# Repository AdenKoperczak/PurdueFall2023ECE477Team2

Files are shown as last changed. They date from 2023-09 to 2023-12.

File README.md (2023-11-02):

# PurdueFall2023ECE477Team2
Code and other files for a desktop Skee-Ball Machine. Our team website can be
found at [https://engineering.purdue.edu/477grp2/](https://engineering.purdue.edu/477grp2/).

# Purdue ECE47700 - Digital Systems Senior Project
This class involves designing a electronics project that could be sold as a 
product. Such a product must involve either a microcontroller or FPGA. More
information can be found at [https://engineering.purdue.edu/ece477/](https://engineering.purdue.edu/ece477/).

# Git Folders and Files
The files in our Git Repository can be broken into two sections: electrical and
code. Electrical design was done in KiCAD 7.0 and includes both schematics and
PCB layouts. Code was done using SystemWorkbench. There are also some other 
code and support files. Bellow is a description of each folder and what it
contains along with some soport files files.

## General Files
- Used Resources.txt: This contains what parts of the microcontroller are being
                      used for what.

## Electrical
- Audio AMP: Contains initial design for our audio amplifier.
- Schematic: Contains the overall schematic and PCB for our design.
- power control: Contains the initial design for our power circuitry.
- sensor: Contains the initial design for our laser break circuit.

## Microcontroller Code
- HUB75Lib: This contains a library and test code to run a 32x64 HUB75 display
            including a font library.
- WS2812BLib: This contains a library and test code for running a WS2812B LED strip.
- SoundLib: This contains a library and test code for generating and playing audio.

## Other Code
- HUB75Font\_Generate: This contains code for generating a font library for the
                       HUB75Lib.

# Project Description
Our project aims to rekindle the nostalgic joy of the traditional Skee-Ball game while
incorporating cutting-edge technology for an enhanced playing experience in the form of
game modes, normal, time attack, and streak. The normal game mode is the same 
as the traditional skate-ball game mode, such that a player would get nine balls and attempt
to score the highest score possible at their own pace, for which the scores per ball are
simply added to get the final score. After they run out of nine balls, any ball they try
to score after would not count, as the game would be over. In time attack mode, the
player sets a time (up to 5 minutes) with an unlimited ball count to score as high as
possible. For the streak mode, the player gets an "unlimited" number of balls as long as
as they score 20 points or higher on the current shot; Once they miss the shot, the score
is finalized. Finally, the timed streak mode combines the time attack with a score.
multiplier, which will go up by 0.1x from 1x every time they make the shot, maxing out at
1.5x and indicated by an LED light bar to the player. Once the player misses a 20+
point shot, the multiplier is reset. The Skee-Ball Machine" is similar to other arcade
machines that you can easily see in arcades; however, they are unaffordable to buy and
are huge in size. Therefore, we specifically designed it to be portable and affordable. 
To make it portable, we replaced the rolling rail into bouncing pad, so the player will 
score the ball by throwing the ball off of the bouncing pad. This device will use a microcontroller,
along with several sensors, buttons, displays, and a speaker to make an iterative game with
different scoring modes to keep the game fresh. In detail, sensors will detect the ball
once they are scored. Also, there will be a speaker, so it will have certain game effects.
sounds when scored through a user-defined amplifier. Also, there will be a display for user 
interfaces to show the score and how much time is left. Finally, we will create a power regulator
to regulate the power supply. We will use a commercial 12V power supply because our speaker 
requires 12V, then we will implement a voltage regulator (buck converter) from 12V commercial 
voltage input to 5V to supply our display, and another linear regulator from 5V to 3.3V to 
supply microprocessors and other components.

## Stretch Goal:
An ability to implement a WS2812B LED-strip to generate some flashing light as a game effect, 
using GPIO pins to operate and a PWM to adjust brightness and frequency to generate certain effect.

## Project Specific Design Requirements (PSDRs):
- PSDR #1 (Hardware): An ability to implement one 32-by-64 column-row
                      matrix display to interface with user, by communicating through GPIO
                      pins from microcontroller. 
- PSDR #2 (Hardware): An ability to implement one 4-by-4 column-row
                      matrix keypad to receive user's input, by communicating through GPIO
                      pins from microcontroller.
- PSDR #3 (Hardware): An ability to generate a soundwave using DAC 
                      from microcontroller and amplify the signal using a user designed
                      audio amplifier to play game effect sounds through a speaker.
- PSDR #4 (Hardware): An ability to implement a step down voltage
                      regulator(buck converter) from 12V commercial voltage input to 5V, and
                      another linear regulator from 5V to 3.3V as we need both 5V and 3.3V
                      to supply different components.
- PSDR #5 (Software): An ability to implement the game logic using system
                      workbench for STM32(eclipse), to properly implement all components, such
                      as optical sensor, display, keypad, and speaker.

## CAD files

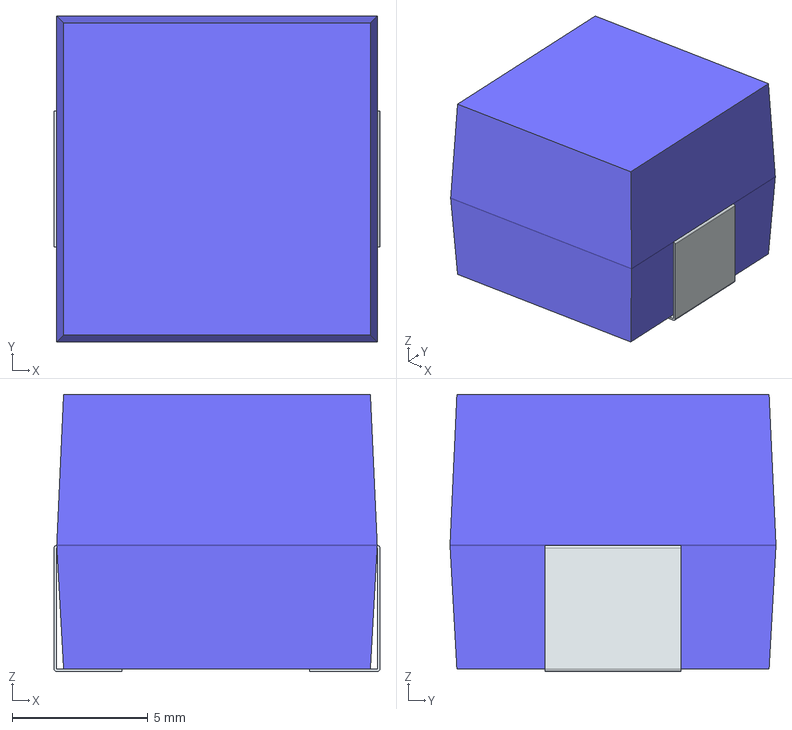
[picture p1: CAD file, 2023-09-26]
Schematic/LIB_MSS1210-103MEB/MSS1210-103MEB/3D/MSS1210-103MEB.stp
12.0 x 12.0 x 10.2 mm
FilletPin1
FilletPin2

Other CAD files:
Schematic/LIB_MSS1210-103MEB/MSS1210-103MEB/Allegro/indpm120120x1020n.psm
Schematic/LIB_MSS1210-103MEB/MSS1210-103MEB/DEHDL/mss1210_103meb/chips/chips.prt

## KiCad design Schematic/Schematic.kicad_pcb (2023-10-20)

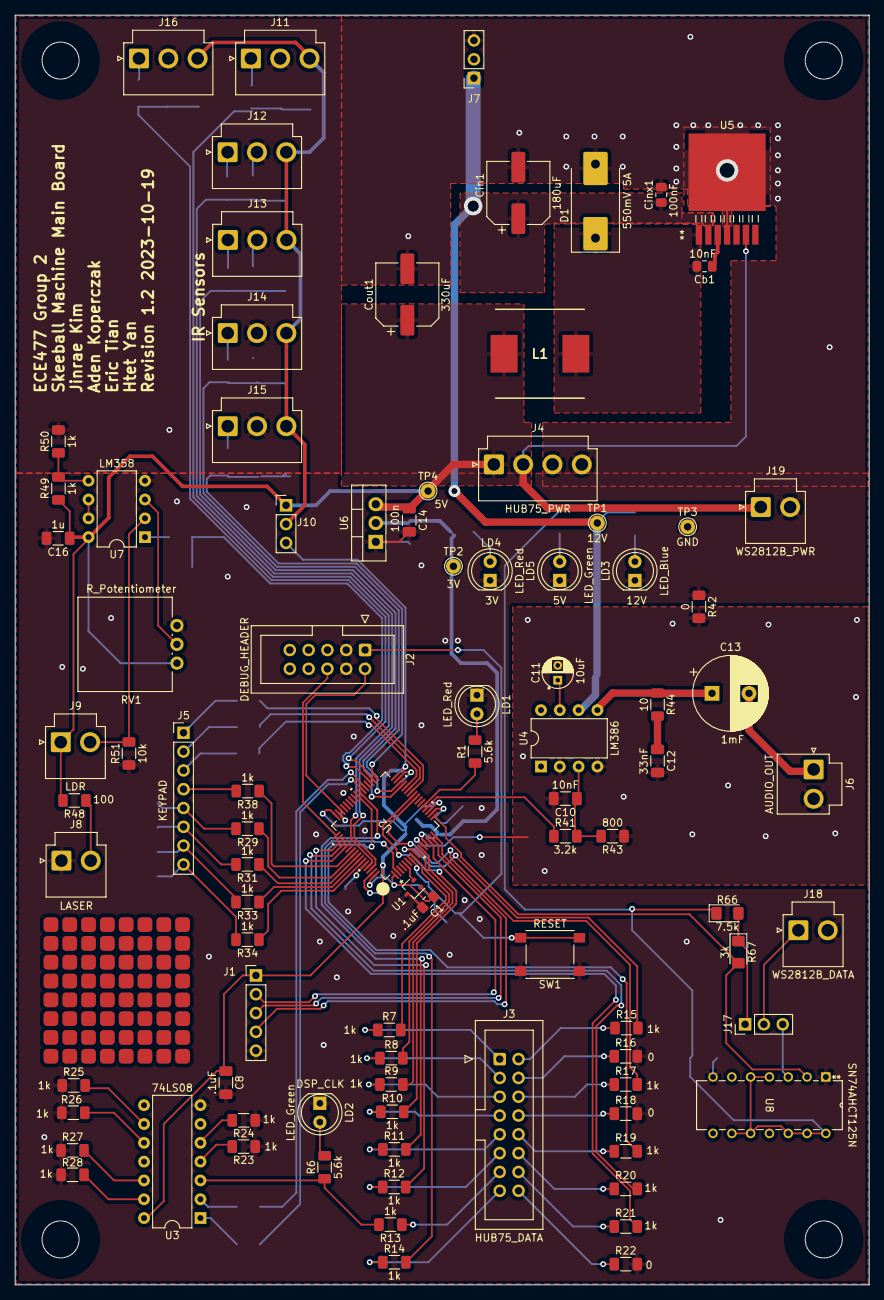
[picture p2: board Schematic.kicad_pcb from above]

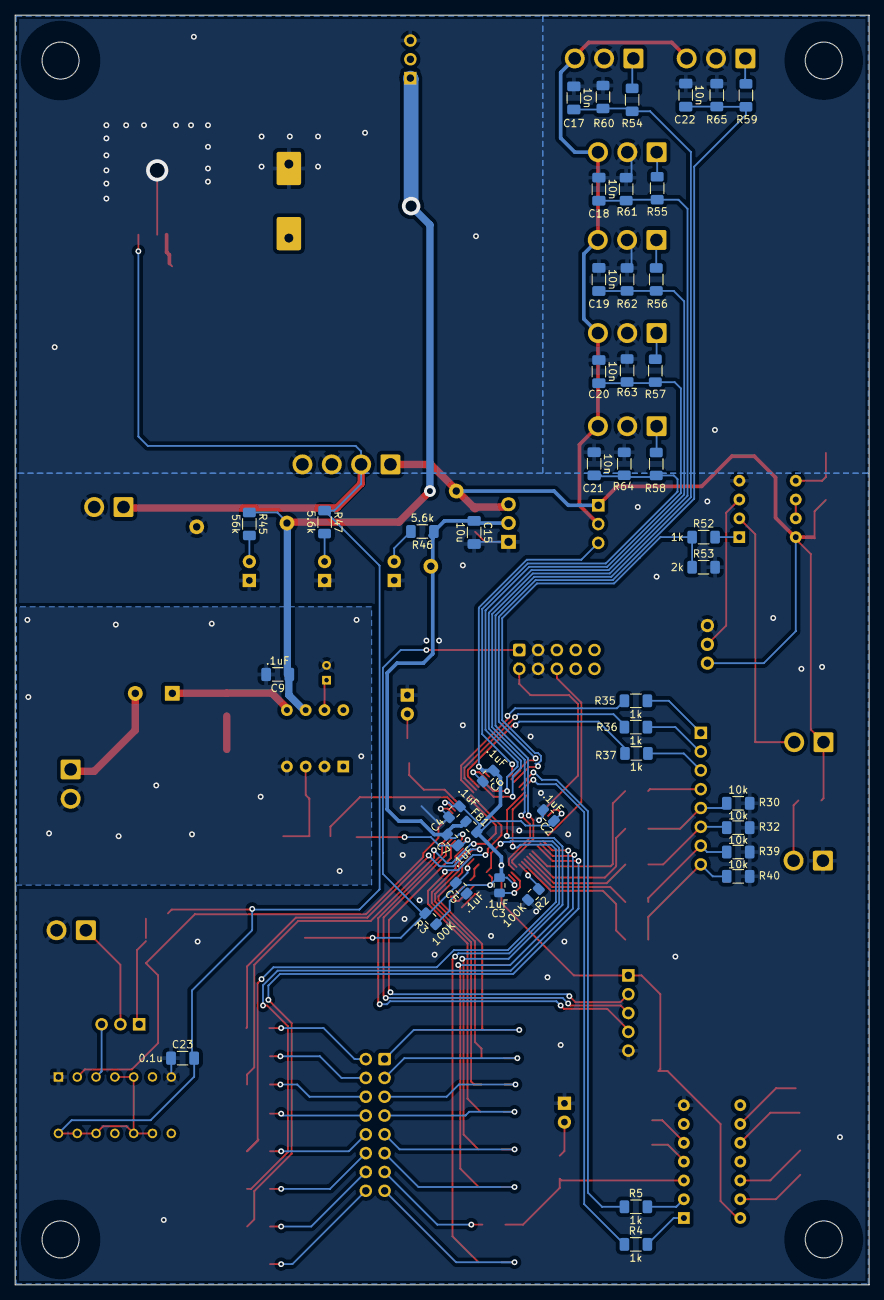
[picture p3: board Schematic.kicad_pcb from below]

Board: 2 copper layers, 115.3 x 171.4 mm, 139 parts (44 on the bottom side), 107 nets.

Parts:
C1, C2, C3, C4, C5, C6, C7: .1uF; C_0805_2012Metric_Pad1.18x1.45mm_HandSolder
C8, C9: .1uF; C_1206_3216Metric_Pad1.33x1.80mm_HandSolder
C10: 10nF; C_1206_3216Metric_Pad1.33x1.80mm_HandSolder
C11: 10uF; CP_Radial_D4.0mm_P2.00mm
C12: 33nF; C_1206_3216Metric_Pad1.33x1.80mm_HandSolder
C13: 1mF; CP_Radial_D10.0mm_P5.00mm
C14: 100n; C_1206_3216Metric_Pad1.33x1.80mm_HandSolder
C15: 10u; C_1206_3216Metric_Pad1.33x1.80mm_HandSolder
C16: 1u; C_1206_3216Metric_Pad1.33x1.80mm_HandSolder
C17, C18, C19, C20, C21, C22: 10n; C_1206_3216Metric_Pad1.33x1.80mm_HandSolder
C23: 0.1u; C_1206_3216Metric_Pad1.33x1.80mm_HandSolder
Cb1: 10nF; C_0805_2012Metric_Pad1.18x1.45mm_HandSolder
Cin1: 180uF; CP_Elec_8x6.9
Cinx1: 100nF; C_0805_2012Metric_Pad1.18x1.45mm_HandSolder
Cout1: 330uF; CP_Elec_8x6.9
D1: 550mV 5A; D_SMC-RM10_Universal_Handsoldering
FB1: Ferrite Bead; L_0805_2012Metric_Pad1.15x1.40mm_HandSolder
H1, H2, H3, H4: MountingHole; MountingHole_5mm
J1: Conn_01x05_Pin; PinHeader_1x05_P2.54mm_Vertical
J2: DEBUG_HEADER; IDC-Header_2x05_P2.54mm_Vertical
J3: HUB75_DATA; IDC-Header_2x08_P2.54mm_Vertical
J4: HUB75_PWR; JST_VH_B4P-VH-B_1x04_P3.96mm_Vertical
J5: KEYPAD; PinHeader_1x08_P2.54mm_Vertical
J6: AUDIO_OUT; JST_VH_B2P-VH-B_1x02_P3.96mm_Vertical
J7: Conn_01x03_Pin; PinSocket_1x03_P2.54mm_Vertical
J8: LASER; JST_VH_B2P-VH-B_1x02_P3.96mm_Vertical
J9: LDR; JST_VH_B2P-VH-B_1x02_P3.96mm_Vertical
J10, J17: Conn_01x03_Pin; PinHeader_1x03_P2.54mm_Vertical
J11, J12, J13, J14, J15, J16: Conn_01x03_Pin; JST_VH_B3P-VH_1x03_P3.96mm_Vertical
J18: WS2812B_DATA; JST_VH_B2P-VH-B_1x02_P3.96mm_Vertical
J19: WS2812B_PWR; JST_VH_B2P-VH-B_1x02_P3.96mm_Vertical
L1: 10uH; INDPM120120X1020N
LD1, LD4: LED_Red; LED_D5.0mm
LD2, LD5: LED_Green; LED_D5.0mm
LD3: LED_Blue; LED_D5.0mm
R1, R6, R46, R47: 5.6k; R_1206_3216Metric_Pad1.30x1.75mm_HandSolder
R2, R3: 100K; C_0805_2012Metric_Pad1.18x1.45mm_HandSolder
R4, R5, R7, R8, R9, R10, R11, R12, R13, R14, R15, R17, R19, R20, R21, R23, R24, R25, R26, R27, R28, R29, R31, R33, R34, R35, R36, R37, R38, R49, R50, R52, R54, R55, R56, R57, R58, R59: 1k; R_1206_3216Metric_Pad1.30x1.75mm_HandSolder
R16, R18, R22, R42: 0; R_1206_3216Metric_Pad1.30x1.75mm_HandSolder
R30, R32, R39, R40, R51: 10k; R_1206_3216Metric_Pad1.30x1.75mm_HandSolder
R41: 3.2k; R_1206_3216Metric_Pad1.30x1.75mm_HandSolder
R43: 800; R_1206_3216Metric_Pad1.30x1.75mm_HandSolder
R44: 10; R_1206_3216Metric_Pad1.30x1.75mm_HandSolder
R45: 56k; R_1206_3216Metric_Pad1.30x1.75mm_HandSolder
R48: 100; R_1206_3216Metric_Pad1.30x1.75mm_HandSolder
R53, R60, R61, R62, R63, R64, R65: 2k; R_1206_3216Metric_Pad1.30x1.75mm_HandSolder
R66: 7.5k; LED_1206_3216Metric_Pad1.42x1.75mm_HandSolder
R67: 3k; LED_1206_3216Metric_Pad1.42x1.75mm_HandSolder
RV1: R_Potentiometer; Potentiometer_Vishay_148-149_Single_Vertical
SW1: RESET; SW_SPST_PTS645
TP1: 12V; TestPoint_THTPad_D2.0mm_Drill1.0mm
TP2: 3V; TestPoint_THTPad_D2.0mm_Drill1.0mm
TP3: GND; TestPoint_THTPad_D2.0mm_Drill1.0mm
TP4: 5V; TestPoint_THTPad_D2.0mm_Drill1.0mm
U1: MAX7375AXR805; SOT-323_SC-70
U2: STM32F091RCT6; LQFP64-10x10mm_STM
U3: 74LS08; DIP-14_W7.62mm
U4: LM386; DIP-8_W7.62mm
U5: LM2678S-12; TS7B
U6: LD1117S33TR_SOT223; TO-220-3_Vertical
U7: LM358; DIP-8_W7.62mm
U8: SN74AHCT125N; N14

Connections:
+3V0: C1.1, C2.1, C3.1, C4.1, C6.1, C8.1, FB1.2, J1.1, J10.3, R3.1, U1.1 (V+), U2.1 (VBAT), U2.19 (VDD), U2.32 (VDD), U2.48 (VDDIO2), U2.64 (VDD), U3.14 (VCC)
+5V: C14.1, C16.1, C23.2, Cout1.1, J4.1, J4.2, J9.1, J10.1, J19.1, L1.2, R47.1, R48.2, R49.1, R66.1, RV1.3, TP4.1, U5.6 (FB), U6.3 (VI), U7.8 (V+), U8.4 (*2OE), U8.5 (2A), U8.9 (3A), U8.10 (*3OE), U8.12 (4A), U8.13 (*4OE), U8.14 (VCC)
+12V: C9.1, Cin1.1, Cinx1.1, J7.1, R45.1, TP1.1, U4.6 (V+), U5.2 (VIN)
/Sensors/Vsens: J10.2, J11.3, J12.3, J13.3, J14.3, J15.3, J16.3
/WS2812B/WS_DATA_RES: J17.1, R66.2, R67.1
/WS2812B/WS_DATA_SHIFTER: J17.3, U8.3 (1Y)
/microprocessor/BOOT0: R2.1, U2.60 (PF11-BOOT0)
/microprocessor/NRST: C5.1, J2.1, R3.2, SW1.2, U2.7 (NRST)
/microprocessor/SWCLK_IN: J2.6, U2.49 (PA14)
/microprocessor/SWDIO_IN: J2.2, U2.46 (PA13)
/power/VSW: Cb1.2, D1.1 (K), L1.1, U5.1 (VSW)
GND: C1.2, C2.2, C3.2, C4.2, C5.2, C6.2, C8.2, C14.2, C15.2, C16.2, C17.2, C18.2, C19.2, C20.2, C21.2, C22.2, C23.1, Cin1.2, Cinx1.2, Cout1.2, D1.2 (A), J1.5, J2.3, J2.4, J4.3, J4.4, J7.3, J8.1, J11.2, J12.2, J13.2, J14.2, J15.2, J16.2, J18.2, J19.2, LD1.1 (K), LD2.1 (K), LD3.1 (K), LD4.1 (K), LD5.1 (K), R2.2, R16.2, R18.2, R22.2, R23.1, R24.1, R25.1, R26.1, R27.1, R28.1, R30.1, R32.1, R39.1, R40.1, R42.1, R50.2, R51.1, R53.2, R60.2, R61.2, R62.2, R63.2, R64.2, R65.2, RV1.1, SW1.1, TP3.1, U1.3 (GND), U2.18 (VSS), U2.31 (VSS), U2.47 (VSS), U2.63 (VSS), U3.7 (GND), U5.4 (GND), U5.8 (TAB), U6.1 (GND), U7.4 (V-), U8.1 (*1OE), U8.7 (GND)
GNDA: C7.2, C9.2, C10.2, C11.2, C12.2, J6.2, R42.2, R43.1, U2.12 (VSSA), U4.2 (-), U4.4 (GND)
unnamed: C12.1, R44.2
unnamed: C13.1, R44.1, U4.5
unnamed: J3.1, R7.1
unnamed: J3.2, R15.1
unnamed: J3.3, R8.1
unnamed: J3.4, R16.1
unnamed: J3.5, R9.1
unnamed: J3.6, R17.1
unnamed: J3.7, R10.1
unnamed: J3.8, R18.1
unnamed: J3.9, R11.1
unnamed: J3.10, R19.1
unnamed: J3.11, R12.1
unnamed: J3.12, R20.1
unnamed: J3.13, R13.1
unnamed: J3.14, R21.1
unnamed: J3.15, R14.1
unnamed: J3.16, R22.1
unnamed: J5.1, R35.2
unnamed: J5.2, R36.2
unnamed: J5.3, R37.2
unnamed: J5.4, R38.2
unnamed: J5.5, R29.2, R30.2
unnamed: J5.6, R31.2, R32.2
unnamed: J5.7, R33.2, R39.2
unnamed: J5.8, R34.2, R40.2
unnamed: C13.2, J6.1
unnamed: J8.2, R48.1
unnamed: J9.2, R51.2, U7.2 (-)
unnamed: J11.1, R54.2
unnamed: J12.1, R55.2
unnamed: J13.1, R56.2
unnamed: J14.1, R57.2
unnamed: J15.1, R58.2
unnamed: J16.1, R59.2
unnamed: J17.2, J18.1
unnamed: LD1.2 (A), R1.2
unnamed: LD2.2 (A), R6.2
unnamed: LD3.2 (A), R45.2
unnamed: LD4.2 (A), R46.2
unnamed: LD5.2 (A), R47.2
unnamed: R4.2, U3.1
unnamed: R5.2, U3.2
unnamed: R6.1, R13.2, U3.3
unnamed: R23.2, U3.4
unnamed: R24.2, U3.5
unnamed: R25.2, U3.9
unnamed: R26.2, U3.10
unnamed: R27.2, U3.12
unnamed: R28.2, U3.13
unnamed: R52.2, U7.1
unnamed: U1.2 (CLOCK), U2.5 (PF0-OSC_IN)
unnamed: R1.1, U2.21 (PA5)
unnamed: C10.1, R41.2, R43.2, U4.3 (+)
unnamed: C11.1, U4.7 (BYPASS)
unnamed: Cb1.1, U5.3 (CB)
unnamed: RV1.2, U7.3 (+)
unnamed: R49.2, R50.1, U7.5 (+)
unnamed: U7.6 (-), U7.7
PA0: J1.2, U2.14 (PA0)
PA1: J1.3, U2.15 (PA1)
PA2: J1.4, U2.16 (PA2)
PA3: R67.2, U2.17 (PA3), U8.2 (1A)
PA4: R41.1, U2.20 (PA4)
PB0: R35.1, U2.26 (PB0)
PB1: R36.1, U2.27 (PB1)
PB2: R37.1, U2.28 (PB2)
PB3: R38.1, U2.55 (PB3)
PB4: R29.1, U2.56 (PB4)
PB5: R31.1, U2.57 (PB5)
PB6: R33.1, U2.58 (PB6)
PB7: R34.1, U2.59 (PB7)
PB8: C17.1, R54.1, R60.1, U2.61 (PB8)
PB9: C18.1, R55.1, R61.1, U2.62 (PB9)
PB10: C19.1, R56.1, R62.1, U2.29 (PB10)
PB11: C20.1, R57.1, R63.1, U2.30 (PB11)
PB12: C21.1, R58.1, R64.1, U2.33 (PB12)
PB13: C22.1, R59.1, R65.1, U2.34 (PB13)
PB14: R52.1, R53.1, U2.35 (PB14)
PC0: R7.2, U2.8 (PC0)
PC1: R15.2, U2.9 (PC1)
PC2: R8.2, U2.10 (PC2)
PC3: R9.2, U2.11 (PC3)
PC4: R17.2, U2.24 (PC4)
PC5: R10.2, U2.25 (PC5)
PC6: R5.1, U2.37 (PC6)
PC7: R4.1, U2.38 (PC7)
PC8: R11.2, U2.39 (PC8)
PC9: R19.2, U2.40 (PC9)
PC10: R12.2, U2.51 (PC10)
PC11: R20.2, U2.52 (PC11)
PC12: R21.2, U2.53 (PC12)
PC13: R14.2, U2.2 (PC13)
Vin: C7.1, C15.1, FB1.1, R46.1, TP2.1, U2.13 (VDDA), U6.2 (VO)

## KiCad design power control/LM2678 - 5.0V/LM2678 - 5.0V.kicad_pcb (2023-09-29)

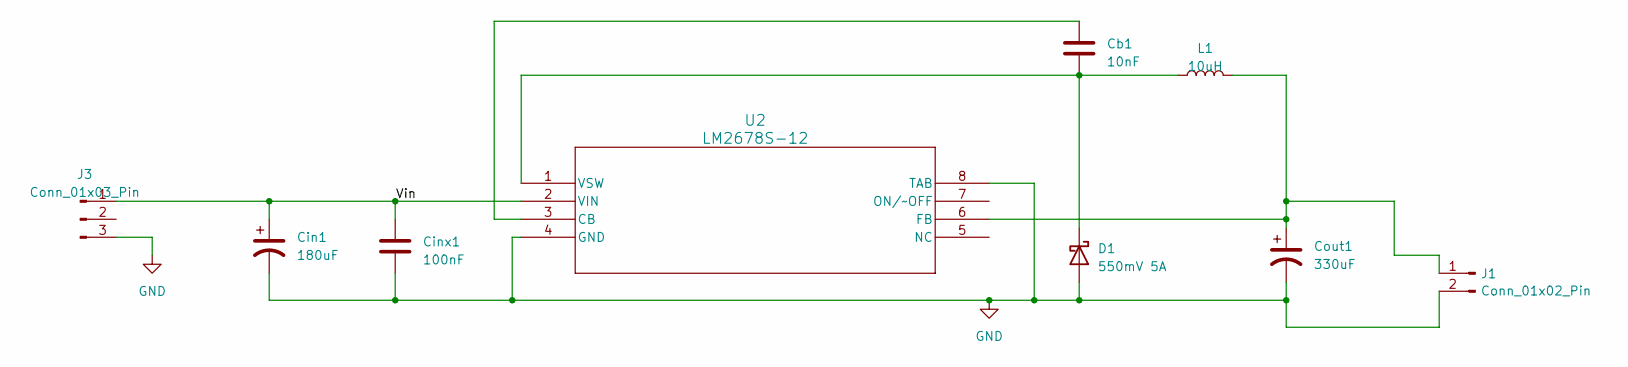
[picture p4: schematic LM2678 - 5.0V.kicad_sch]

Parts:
Cb1: 10nF; C_0805_2012Metric_Pad1.18x1.45mm_HandSolder
Cin1: 180uF; CP_Elec_8x6.9
Cinx1: 100nF; C_0805_2012Metric_Pad1.18x1.45mm_HandSolder
Cout1: 330uF; CP_Elec_8x6.9
D1: 550mV 5A; D_SMC-RM10_Universal_Handsoldering
J1: Conn_01x02_Pin; PinHeader_1x02_P2.54mm_Vertical
J3: Conn_01x03_Pin; PinHeader_1x03_P2.54mm_Vertical
L1: 10uH; INDPM120120X1020N
U2: LM2678S-12; TS7B

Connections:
/Vin: Cin1.1, Cinx1.1, J3.1, U2.2 (VIN)
GND: Cin1.2, Cinx1.2, Cout1.2, D1.2 (A), J1.2, J3.3, U2.4 (GND), U2.8 (TAB)
unnamed: Cb1.2, D1.1 (K), L1.1, U2.1 (VSW)
unnamed: Cout1.1, J1.1, L1.2, U2.6 (FB)
unnamed: Cb1.1, U2.3 (CB)

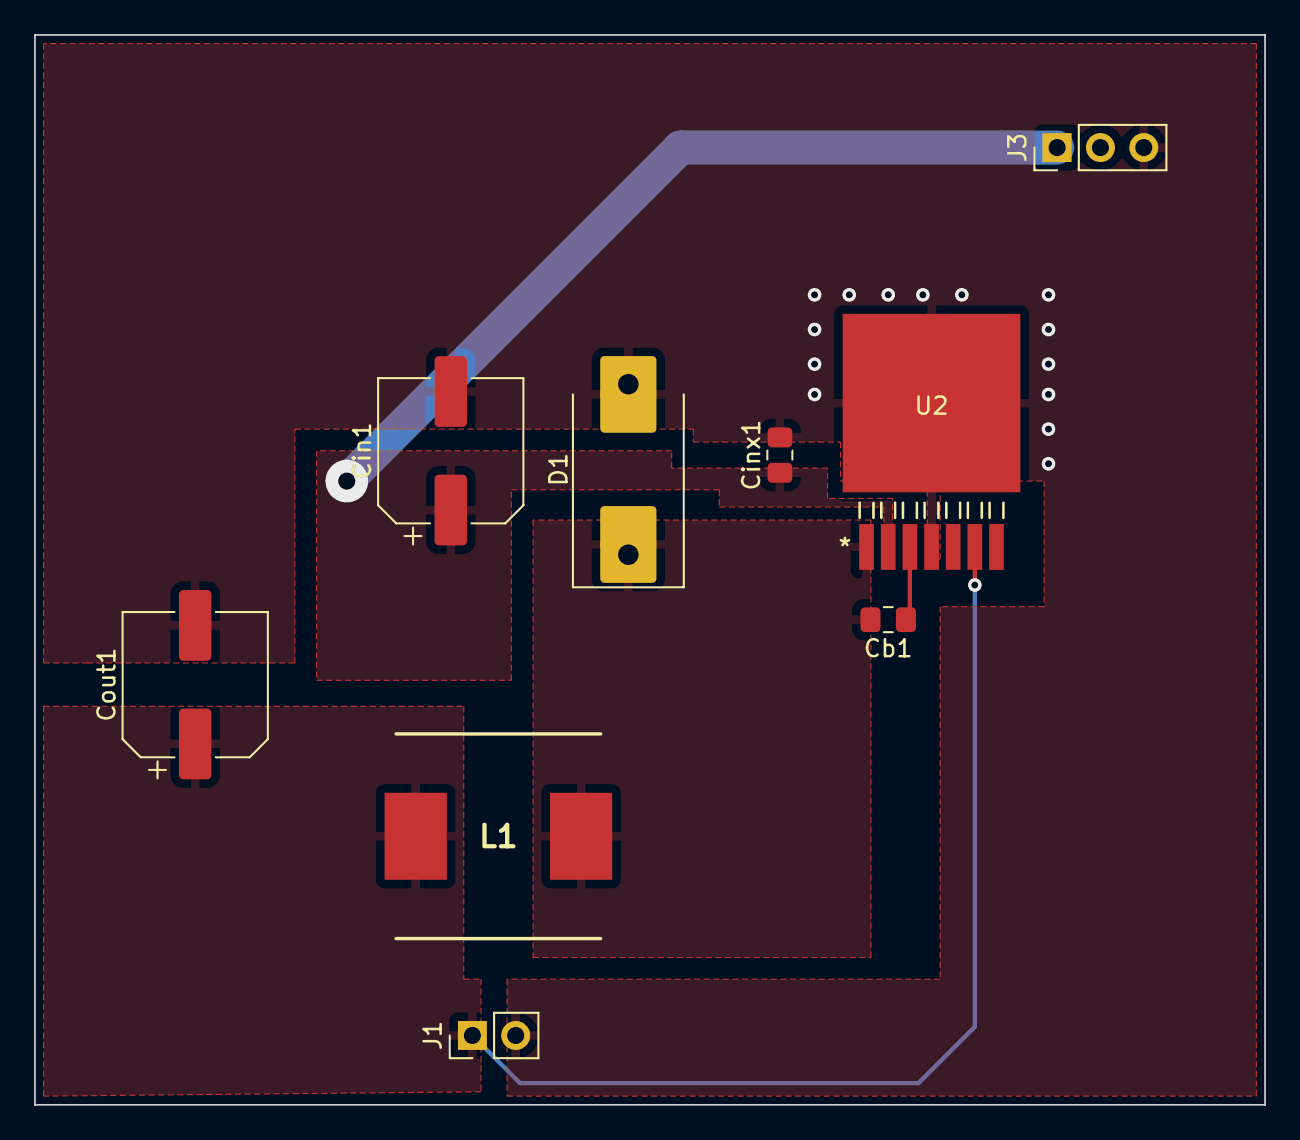
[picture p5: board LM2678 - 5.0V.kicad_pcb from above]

Board: 2 copper layers, 72.1 x 62.7 mm, 9 parts (0 on the bottom side), 5 nets.

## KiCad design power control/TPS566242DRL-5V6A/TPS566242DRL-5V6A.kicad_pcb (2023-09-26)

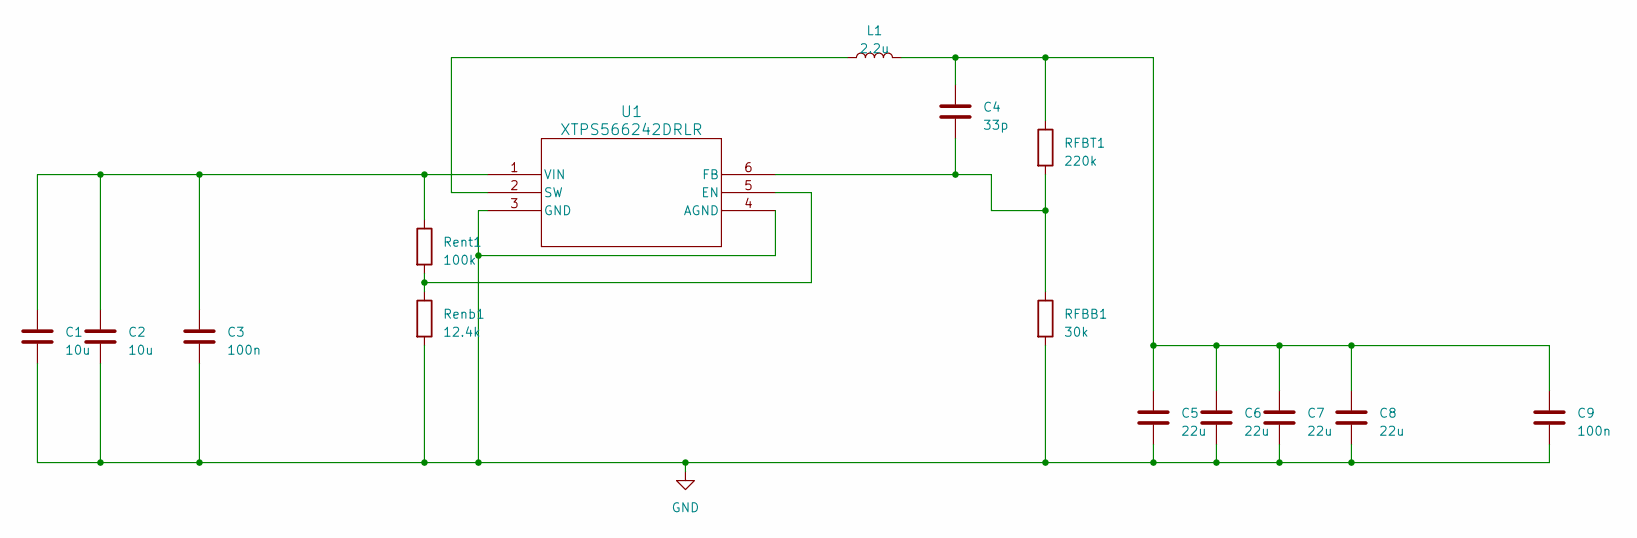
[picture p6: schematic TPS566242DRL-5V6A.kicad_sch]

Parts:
C1, C2: 10u; C_0805_2012Metric_Pad1.18x1.45mm_HandSolder
C3, C9: 100n; C_0603_1608Metric_Pad1.08x0.95mm_HandSolder
C4: 33p; C_0402_1005Metric_Pad0.74x0.62mm_HandSolder
C5, C6, C7, C8: 22u; C_0805_2012Metric_Pad1.18x1.45mm_HandSolder
L1: 2.2u; L_Coilcraft_XAL5030-XXX
RFBB1: 30k; R_0603_1608Metric_Pad0.98x0.95mm_HandSolder
RFBT1: 220k; R_0603_1608Metric_Pad0.98x0.95mm_HandSolder
Renb1: 12.4k; R_0402_1005Metric_Pad0.72x0.64mm_HandSolder
Rent1: 100k; R_0402_1005Metric_Pad0.72x0.64mm_HandSolder
U1: XTPS566242DRLR; SOT6_DRL_TEX

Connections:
GND: C1.2, C2.2, C3.2, C5.2, C6.2, C7.2, C8.2, C9.2, RFBB1.2, Renb1.2, U1.3 (GND), U1.4 (AGND)
unnamed: C4.1, C5.1, C6.1, C7.1, C8.1, C9.1, L1.2, RFBT1.1
unnamed: Renb1.1, Rent1.2, U1.5 (EN)
unnamed: C4.2, RFBB1.1, RFBT1.2, U1.6 (FB)
unnamed: L1.1, U1.2 (SW)
unnamed: C1.1, C2.1, C3.1, Rent1.1, U1.1 (VIN)

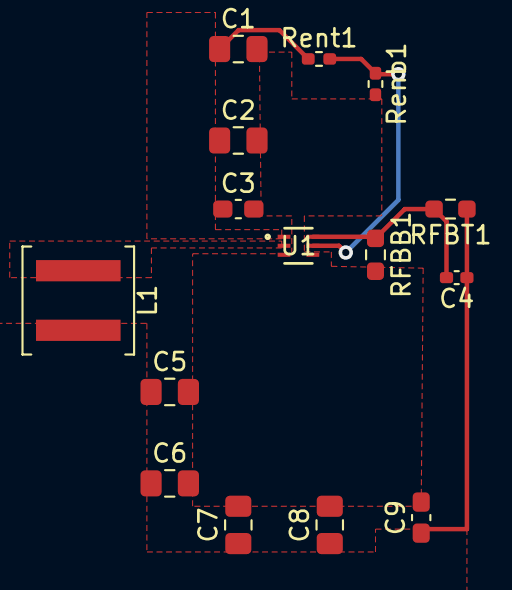
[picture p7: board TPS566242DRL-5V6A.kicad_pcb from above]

Board: 2 copper layers, 15 parts (0 on the bottom side), 6 nets.

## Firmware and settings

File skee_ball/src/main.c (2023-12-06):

#include "ws2812b.h"
#include "HUB75.h"
#include "HUB75_font.h"
#include "SoundLib.h"
#include "keypad.h"
#include "sensors.h"
#include "GameLogic.h"
#include "colors.h"
#include "stm32f0xx.h"

int lastKey;
int doSound;
int softOff;

#define NORMAL_BALL_COUNT 9
#define TIME_MAX_TIME (5*60)
#define MAX_SCORE 99999

#define COMBO_MULTI_DEN 2
#define COMBO_MULTI_INC 1
#define COMBO_MULTI_MAX ((int)(COMBO_MULTI_DEN * 5))


const uint8_t multi_colors[][3] = {
		{1, 0, 0},
		{1, 1, 0},
		{0, 1, 0}
};

GameModes gameMode;
GameState gameState;

uint32_t  gameScore;

uint32_t  gameEndTime;
uint32_t  gameTime;

ScoreType gameStreakType;
uint32_t  gameMulti;
uint32_t  gameBallCnt;

char timeBuffer[4];

void render_score() {
	if (gameScore > MAX_SCORE) {
		gameScore = MAX_SCORE;
	}
	hub75_font_render_str("SCORE", 1, 1, 1, 1, 1, 0, 0, 0);
	hub75_font_render_int(gameScore, 0, 34, 1, SCORE_COLOR, 0, 0, 0);
}

void render_ball_count() {
	hub75_font_render_str("BALLS", 1, 9, 1, 1, 1, 0, 0, 0);
	hub75_font_render_int(gameBallCnt, 0, 34, 9, BALL_COUNT_COLOR, 0, 0, 0);
}

void render_timer() {
	int time = (gameEndTime - gameTime) / GAME_SECOND;

	hub75_font_render('0' + time / 60,         1, 9, TIMER_COLOR, 0, 0, 0);
	hub75_font_render(':',                     6, 9, TIMER_COLOR, 0, 0, 0);
	hub75_font_render('0' + (time % 60) / 10, 11, 9, TIMER_COLOR, 0, 0, 0);
	hub75_font_render('0' + (time % 10),      17, 9, TIMER_COLOR, 0, 0, 0);

	if (time <= TIMER_FAST_FLASH) {
		lights_set_mode(L_Mode_Fast_Flash, TIMER_FAST_FLASH_COLOR);
	} else if (time <= TIMER_SLOW_FLASH) {
		lights_set_mode(L_Mode_Slow_Flash, TIMER_SLOW_FLASH_COLOR);
	}
}

void render_back() {
	for (int x = 0; x < HUB75_WIDTH; x++) {
		for (int y = 0; y < HUB75_HIEGHT; y++) {
			hub75_set_pixel(x, y, 0, 0, 0);
		}
	}
}

void render_mode_select() {
	render_back();
	hub75_font_render_str("SELECT A", 1,  1, 1, 1, 1, 0, 0, 0);
	hub75_font_render_str("MODE",     1,  9, 1, 1, 1, 0, 0, 0);
	hub75_font_render('A',  1, 17, MODE_NORMAL_COLOR,      0, 0, 0);
	hub75_font_render('B', 10, 17, MODE_TIME_ATTACK_COLOR, 0, 0, 0);
	hub75_font_render('C', 19, 17, MODE_STREAK_COLOR,      0, 0, 0);
	hub75_font_render('D', 28, 17, MODE_COMBO_COLOR,       0, 0, 0);

	if (!doSound) {
		hub75_font_render('M', 58, 23, 1, 1, 1, 0, 0, 0);
	}

	lights_set_mode(L_Mode_Select, 0, 0, 0);
}

void render_confirmation() {
	render_back();
	hub75_font_render_str("PLAY", 1, 1, 1, 1, 1, 0, 0, 0);
	switch (gameMode) {
	case Mode_Normal:
		hub75_font_render_str("NORMAL", 1, 9, MODE_NORMAL_COLOR, 0, 0, 0);
		lights_set_mode(L_Mode_Solid, MODE_NORMAL_COLOR);
		break;
	case Mode_Time_Attack:
		hub75_font_render_str("TIME",    1, 9, MODE_TIME_ATTACK_COLOR, 0, 0, 0);
		hub75_font_render_str("ATTACK", 28, 9, MODE_TIME_ATTACK_COLOR, 0, 0, 0);
		lights_set_mode(L_Mode_Solid, MODE_TIME_ATTACK_COLOR);
		break;
	case Mode_Streak:
		hub75_font_render_str("STREAK", 1, 9, MODE_STREAK_COLOR, 0, 0, 0);
		lights_set_mode(L_Mode_Solid, MODE_STREAK_COLOR);
		break;
	case Mode_Combo:
		hub75_font_render_str("COMBO", 1, 9, MODE_COMBO_COLOR, 0, 0, 0);
		lights_set_mode(L_Mode_Solid, MODE_COMBO_COLOR);
		break;
	default:
		hub75_font_render_str("INVALID", 1, 9, 1, 1, 1, 0, 0, 0);
		lights_set_mode(L_Mode_Slow_Flash, 0xff, 0xff, 0xff);
		break;
	}

	hub75_font_render_str("MODE", 1, 17, 1, 1, 1, 0, 0, 0);

}

void render_time_buffer() {
	hub75_font_render(timeBuffer[2],  1, 9, 1, 1, 1, 0, 0, 0);
	hub75_font_render(':',            6, 9, 1, 1, 1, 0, 0, 0);
	hub75_font_render(timeBuffer[1], 11, 9, 1, 1, 1, 0, 0, 0);
	hub75_font_render(timeBuffer[0], 17, 9, 1, 1, 1, 0, 0, 0);
}

void render_time_input() {
	hub75_font_render_str("ENTER TIME", 1, 1, 1, 1, 1, 0, 0, 0);

	render_time_buffer();
}

void render_final_score() {
	render_back();
	render_score();

	switch (gameMode) {
	case Mode_Normal:
		lights_set_mode(L_Mode_Slow_Flash, MODE_NORMAL_COLOR);
		hub75_font_render_str("GAME OVER", 1,  9, GAME_OVER_COLOR, 0, 0, 0);
		break;
	case Mode_Time_Attack:
		render_time_buffer();
		hub75_font_render_str("GAME OVER", 1,  17, GAME_OVER_COLOR, 0, 0, 0);
		lights_set_mode(L_Mode_Slow_Flash, MODE_TIME_ATTACK_COLOR);
		break;
	case Mode_Streak:
		render_ball_count();
		hub75_font_render_str("GAME OVER", 1,  17, GAME_OVER_COLOR, 0, 0, 0);
		lights_set_mode(L_Mode_Slow_Flash, MODE_STREAK_COLOR);
		break;
	case Mode_Combo:
		render_time_buffer();
		hub75_font_render_str("GAME OVER", 1,  17, GAME_OVER_COLOR, 0, 0, 0);
		lights_set_mode(L_Mode_Slow_Flash, MODE_COMBO_COLOR);
		break;
	default:
		hub75_font_render_str("INVALID", 1, 17, 1, 1, 1, 0, 0, 0);
		lights_set_mode(L_Mode_Slow_Flash, GAME_OVER_COLOR);
		break;
	}

}


void render_multi() {

	switch (gameStreakType) {
	case Score_10:
		hub75_font_render_str(" 10X", 1, 17, 1, 1, 1, 0, 0, 0);
		break;
	case Score_20:
		hub75_font_render_str(" 20X", 1, 17, 1, 1, 1, 0, 0, 0);
		break;
	case Score_30:
		hub75_font_render_str(" 30X", 1, 17, 1, 1, 1, 0, 0, 0);
		break;
	case Score_50:
		hub75_font_render_str("100X", 1, 17, 1, 1, 1, 0, 0, 0);
		break;
	case Score_Gutter:
		hub75_font_render_str("  0X", 1, 17, 1, 1, 1, 0, 0, 0);
		break;
	}
	int whole = gameMulti / COMBO_MULTI_DEN;
	int frac  = ((gameMulti * 10) / COMBO_MULTI_DEN) % 10;


	hub75_font_render('.',            30, 17, 1, 1, 1, 0, 0, 0); // rendered first because it overlaps
	hub75_font_render_int_n(whole, 1, 25, 17, 1, 1, 1, 0, 0, 0);
	hub75_font_render_int_n(frac,  1, 35, 17, 1, 1, 1, 0, 0, 0);

	for (int i = MULTI_BAR_LEFT; i < MULTI_BAR_RIGHT; i++) {
		if (i * (COMBO_MULTI_MAX - COMBO_MULTI_DEN) < (gameMulti - COMBO_MULTI_DEN) * HUB75_WIDTH) {
			int index = (i - MULTI_BAR_LEFT) * sizeof(multi_colors) / sizeof(multi_colors[0]) / (MULTI_BAR_RIGHT - MULTI_BAR_LEFT);
			hub75_set_pixel(i, HUB75_HIEGHT - 2, multi_colors[index][0], multi_colors[index][1], multi_colors[index][2]);
			hub75_set_pixel(i, HUB75_HIEGHT - 3, multi_colors[index][0], multi_colors[index][1], multi_colors[index][2]);
		} else {
			hub75_set_pixel(i, HUB75_HIEGHT - 2, 0, 0, 0);
			hub75_set_pixel(i, HUB75_HIEGHT - 3, 0, 0, 0);
		}

		hub75_set_pixel(i, HUB75_HIEGHT - 4, 1, 1, 1);
		hub75_set_pixel(i, HUB75_HIEGHT - 1, 1, 1, 1);
	}
}

int parse_time() {
	int total = 0;

	total += (timeBuffer[0] - '0') * 1;
	total += (timeBuffer[1] - '0') * 10;
	total += (timeBuffer[2] - '0') * 60;
	total += (timeBuffer[3] - '0') * 600;

	return total;
}

void update_input_time_back() {
	timeBuffer[0] = timeBuffer[1];
	timeBuffer[1] = timeBuffer[2];
	timeBuffer[2] = timeBuffer[3];
	timeBuffer[3] = '0';
}

void update_input_time(char c) {
	timeBuffer[3] = timeBuffer[2];
	timeBuffer[2] = timeBuffer[1];
	timeBuffer[1] = timeBuffer[0];
	timeBuffer[0] = c;

	int time = parse_time();

	if (time > TIME_MAX_TIME) {
		update_input_time_back();
	}
}


void start_normal() {
	gameBallCnt = NORMAL_BALL_COUNT;
	gameScore   = 0;

	render_back();
	render_score();
	render_ball_count();
	lights_set_mode(L_Mode_Chase, MODE_NORMAL_COLOR);
}

void score_normal(ScoreType scoreType) {
	gameBallCnt--;
	if (gameBallCnt == 0) {
		gameState = Game_Final_Score;
	}

	switch (scoreType) {
	case Score_Gutter:
		sound_gutter();
		break;
	case Score_10:
		sound_10();
		gameScore += 10;
		break;
	case Score_20:
		sound_20();
		gameScore += 20;
		break;
	case Score_30:
		sound_30();
		gameScore += 30;
		break;
	case Score_50:
		sound_50();
		gameScore += 100;
		break;
	}

	if (gameState == Game_Final_Score) {
		render_final_score();
	} else {
		render_ball_count();
		render_score();
	}
}

void start_time_attack() {
	gameEndTime = gameTime + parse_time() * GAME_SECOND;
	gameScore   = 0;

	render_back();
	render_score();
	lights_set_mode(L_Mode_Chase, MODE_TIME_ATTACK_COLOR);
}

void score_time_attack(ScoreType scoreType) {
	switch (scoreType) {
	case Score_Gutter:
		sound_gutter();
		break;
	case Score_10:
		sound_10();
		gameScore += 10;
		break;
	case Score_20:
		sound_20();
		gameScore += 20;
		break;
	case Score_30:
		sound_30();
		gameScore += 30;
		break;
	case Score_50:
		sound_50();
		gameScore += 100;
		break;
	}

	render_score();
}

void start_streak() {
	gameScore = 0;
	gameBallCnt = 0;

	render_back();
	render_score();
	lights_set_mode(L_Mode_Chase, MODE_STREAK_COLOR);
}

void score_streak(ScoreType scoreType) {
	switch (scoreType) {
	case Score_Gutter:
	case Score_10:
		sound_gutter();
		gameState = Game_Final_Score;
		break;
	case Score_20:
		sound_20();
		gameScore += 20;
		break;
	case Score_30:
		sound_30();
		gameScore += 30;
		break;
	case Score_50:
		sound_50();
		gameScore += 100;
		break;
	}

	if (gameState == Game_Final_Score) {
		render_final_score();
	} else {
		gameBallCnt++;
		render_score();
	}

}

void start_combo() {
	gameScore = 0;
	gameMulti = COMBO_MULTI_DEN;
	gameStreakType = Score_Gutter;
	gameEndTime = gameTime + parse_time() * GAME_SECOND;

	render_back();
	render_score();
	render_multi();
	render_timer();
	lights_set_mode(L_Mode_Chase, MODE_COMBO_COLOR);
}

void score_combo(ScoreType scoreType) {
	if (scoreType == gameStreakType && scoreType != Score_Gutter) {
		gameMulti += COMBO_MULTI_INC;
		if (gameMulti > COMBO_MULTI_MAX) {
			gameMulti = COMBO_MULTI_MAX;
		}
	} else {
		gameMulti = COMBO_MULTI_DEN;
		gameStreakType = scoreType;
	}


	switch (scoreType) {
	case Score_Gutter:
		sound_gutter();
		break;
	case Score_10:
		sound_10();
		gameScore += 10 / COMBO_MULTI_DEN * gameMulti;
		break;
	case Score_20:
		sound_20();
		gameScore += 20 / COMBO_MULTI_DEN * gameMulti;
		break;
	case Score_30:
		sound_30()
		gameScore += 30 / COMBO_MULTI_DEN * gameMulti;
		break;
	case Score_50:
		sound_50();
		gameScore += 500 / COMBO_MULTI_DEN * gameMulti;
		break;
	}

	render_score();
	render_multi();
}

void sensors_scored (ScoreType scoreType) {
	if (gameState != Game_Playing) {
		return;
	}
	// actual scoring logic
	switch (gameMode) {
	case Mode_Normal:
		score_normal(scoreType);
		break;
	case Mode_Time_Attack:
		score_time_attack(scoreType);
		break;
	case Mode_Streak:
		score_streak(scoreType);
		break;
	case Mode_Combo:
		score_combo(scoreType);
		break;
	case Mode_None:
	default:
		break;
	}
}

void keypad_callback(int key) {

	if (key == lastKey || lastKey != Keypad_None || key == Keypad_None || key == Keypad_Invl) {
		lastKey = key;
		return;
	}

	key = keypadChars[key];

	switch (gameState) {
	case Game_Mode_Select:
		switch (key) {
		case 'A':
			gameMode  = Mode_Normal;
			break;
		case 'B':
			gameMode  = Mode_Time_Attack;
			break;
		case 'C':
			gameMode  = Mode_Streak;
			break;
		case 'D':
			gameMode  = Mode_Combo;
			break;
		case '1':
			doSound ^= 1;
			render_mode_select();
			lastKey = key;
			return;
		case '2':
			render_back();
			gameState = Game_Off;
			lights_set_mode(L_Mode_Off, 0, 0, 0);
			lastKey = key;
			return;
		default:
			lastKey = key;
			return;
		}
		gameState = Game_Mode_Confirm;
		render_confirmation();
		break;
	case Game_Mode_Confirm:
		if (key == '#') {
			switch(gameMode) {
			case Mode_Normal:
				start_normal();
				gameState = Game_Playing;
				break;
			case Mode_Time_Attack:
				render_back();
				render_time_input();
				gameState = Game_Inputing;
				break;
			case Mode_Streak:
				start_streak();
				gameState = Game_Playing;
				break;
			case Mode_Combo:
				render_back();
				render_time_input();
				gameState = Game_Inputing;
				break;
			default:
				render_mode_select();
				gameState = Game_Mode_Select;
				break;
			}
		} else if (key == '*') {
			render_mode_select();
			gameState = Game_Mode_Select;
		}
		break;
	case Game_Inputing:
		switch (key) {
		case '0':
		case '1':
		case '2':
		case '3':
		case '4':
		case '5':
		case '6':
		case '7':
		case '8':
		case '9':
			update_input_time(key);
			render_time_input();
			break;
		case '*':
			update_input_time_back();
			render_time_input();
			break;
		case '#':
			if (parse_time() > 0) {
				switch (gameMode) {
				case Mode_Time_Attack:
					start_time_attack();
					break;
				case Mode_Combo:
					start_combo();
					break;
				default:
					break;
				}

				gameState = Game_Playing;
			}
			break;
		default:
			break;
		}
		break;
	case Game_Playing:
		if (key == '*') {
			gameState = Game_Final_Score;
			render_final_score();
		}
		break;
	case Game_Final_Score:
		switch (key) {
		case '1':
			switch (gameMode) {
			case Mode_Normal:
				start_normal();
				break;
			case Mode_Streak:
				start_streak();
				break;
			case Mode_Time_Attack:
				start_time_attack();
				break;
			case Mode_Combo:
				start_combo();
				break;
			default:
				break;
			}
			gameState = Game_Playing;
			break;
		default:
			gameState = Game_Mode_Select;
			gameMode  = Mode_None;
			render_mode_select();
			break;
		}
		break;
	case Game_Off:
		render_mode_select();
		gameState = Game_Mode_Select;
		break;
	}

	lastKey = key;
}


int lightsPos;
int lightsColor;

void TIM1_BRK_UP_TRG_COM_IRQHandler() {
	TIM1->SR &= ~TIM_SR_UIF;

	gameTime++;

	if ((gameMode == Mode_Time_Attack || gameMode == Mode_Combo) && gameState == Game_Playing) {
		render_timer();

		if (gameTime == gameEndTime) {
			gameState = Game_Final_Score;
			render_final_score();
		}
	}

	lights_tick();
}

int main(void) {
	gameMode       = Mode_None;
	gameState      = Game_Mode_Select;

	gameScore      = 0;

	gameEndTime    = 0;
	gameTime       = 0;

	gameStreakType = Score_Gutter;
	gameMulti      = 5;
	gameBallCnt    = 9;

	lightsPos  = 0;
	lightsColor = 1;
	doSound = 1;

	lastKey  = Keypad_None;

	timeBuffer[0] = '0';
	timeBuffer[1] = '0';
	timeBuffer[2] = '0';
	timeBuffer[3] = '0';

	ws2812b_init();
	hub75_init(30);
	sound_init();
	keypad_init();
	sensors_init();

	lights_set_mode(L_Mode_Off, 0, 0, 0);

	// TIM1 for game tick

	RCC->APB2ENR |= RCC_APB2ENR_TIM1EN;
	TIM1->DIER  = TIM_DIER_UIE;
	TIM1->PSC   = 48000 / 4 - 1;
	TIM1->ARR   = 125 - 1;
	TIM1->CR1 |= TIM_CR1_CEN;
	NVIC->ISER[0] |= (1 << TIM1_BRK_UP_TRG_COM_IRQn);

	NVIC_SetPriority(TIM1_BRK_UP_TRG_COM_IRQn, 3);

	// HUB75 initial test.
	render_mode_select();

	for(;;) {
		asm volatile ("wfi;");
	}
}

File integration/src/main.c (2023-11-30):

#include "ws2812b.h"
#include "HUB75.h"
#include "HUB75_font.h"
#include "SoundLib.h"
#include "keypad.h"
#include "sensors.h"
#include "GameLogic.h"
#include "stm32f0xx.h"

int number;
int pos;
int wscolor;
int currentTone;

const int tones[][2] = {
		{277, 350},
		{311, 415},
		{330, 392},
		{261, 311},
		{350, 440}
};

int keyCount;
int lastKey;

#define SCORE_X 1
#define SCORE_Y 5

#define BALL_CNT_X 1
#define BALL_CNT_Y 13

GameModes gameMode;
GameState gameState;

uint32_t  gameScore;

uint32_t  gameEndTime;
uint32_t  gameTime;

ScoreType gameStreakType;
uint32_t  gameMulti;
uint32_t  gameBallCnt;

void render_score() {
	hub75_font_render_int_7x5(gameScore, 0, SCORE_X, SCORE_Y, 1, 1, 1, 0, 0, 0);
}

void render_ball_count() {
	hub75_font_render_int_7x5(gameBallCnt, 0, BALL_CNT_X, BALL_CNT_Y, 1, 1, 1, 0, 0, 0);
}

void score_normal(ScoreType scoreType) {
	gameBallCnt--;
	if (gameBallCnt == 0) {
		gameState = Game_Final_Score;
	}

	switch (scoreType) {
	case Score_Gutter:
		break;
	case Score_10:
		gameScore += 10;
		break;
	case Score_20:
		gameScore += 20;
		break;
	case Score_30:
		gameScore += 30;
		break;
	case Score_50:
		gameScore += 50;
		break;
	}

	render_ball_count();
	render_score();
}

void sensors_scored (ScoreType scoreType) {
	if (gameState != Game_Playing) {
		return;
	}
	// actual scoring logic
	switch (gameMode) {
	case Mode_Normal:
		score_normal(scoreType);
		break;
	case Mode_Time_Attack:
		//score_time_attack(scoreType);
		break;
	case Mode_Streak:
		//score_streak(scoreType);
		break;
	case Mode_Combo:
		//score_combo(scoreType);
		break;
	case Mode_None:
	default:
		break;
	}
}

void keypad_callback(int key) {
	switch (key) {
	case Keypad_None:
		hub75_font_render_7x5(' ', HUB75_WIDTH - 7, 5, 1, 1, 0, 0, 0, 0);
		break;
	case Keypad_Invl:
		hub75_font_render_7x5('I', HUB75_WIDTH - 7, 5, 1, 1, 0, 0, 0, 0);
		break;
	default:
		hub75_font_render_7x5(keypadChars[key], HUB75_WIDTH - 7, 5, 1, 1, 0, 0, 0, 0);
		break;
	}

	if (key != Keypad_None && key != Keypad_Invl && lastKey != Keypad_Invl && key != lastKey) {
		keyCount ++;
	}

	lastKey = key;

	//hub75_font_render_int_7x5(keyCount, 0, 1, 16, 1, 1, 0, 0, 0, 0);
}

void TIM1_BRK_UP_TRG_COM_IRQHandler() {

	TIM1->SR &= ~TIM_SR_UIF;

	gameTime++;

	int color = (number % 7) + 1;

	hub75_font_render_int_7x5(number, 1, HUB75_WIDTH - 7, 16, color & 0x4, color & 0x2, color & 0x1, 0, 0, 0);


	if ((number & 0x3) == 0) {
		sound_play(tones[currentTone][0], SOUND_MAX_VOL, tones[currentTone][1], SOUND_MAX_VOL, Sound_Mixed, SOUND_SECOND * 0.5);
		currentTone++;
		if (currentTone == sizeof(tones) / sizeof(tones[0])) {
			currentTone = 0;
		}
	}


	TIM3->SR &= ~TIM_SR_UIF;

	if (pos == 66) {
		pos = 0;
		wscolor = wscolor + 1;

		if (wscolor == 64) {
			wscolor = 1;
		}
	}



	ws2812b_setpixel(pos, (wscolor << (7 - 3)) & 0xc0,
			              (wscolor << (7 - 1)) & 0xc0,
						  (wscolor << (7 - 0)) & 0xc0);

	ws2812b_refresh();
	pos++;

	number += 1;
}

int main(void) {
	gameMode       = Mode_Normal;
	gameState      = Game_Playing;

	gameScore      = 0;

	gameEndTime    = 0;
	gameTime       = 0;

	gameStreakType = Score_Gutter;
	gameMulti      = 5;
	gameBallCnt    = 1000;

	pos = 0;
	wscolor = 1;
	number = 0;
	keyCount = 0;
	lastKey  = Keypad_None;

	ws2812b_init();
	hub75_init(30);
	sound_init();
	keypad_init();
	sensors_init();


	// HUB75 initial test.

	for (int x = 0; x < HUB75_WIDTH; x++) {
		hub75_set_pixel(x, 0, x & 1, x & 2, x & 4);
		hub75_set_pixel(x, 1, 1, 0, 0);
		hub75_set_pixel(x, 2, 0, 1, 0);
		hub75_set_pixel(x, 3, 0, 0, 1);

		hub75_set_pixel(x, HUB75_HIEGHT - 1 - 3, 0, 0, 1);
		hub75_set_pixel(x, HUB75_HIEGHT - 1 - 2, 0, 1, 0);
		hub75_set_pixel(x, HUB75_HIEGHT - 1 - 1, 1, 0, 0);
		hub75_set_pixel(x, HUB75_HIEGHT - 1 - 0, x & 1, x & 2, x & 4);

	}

	//hub75_font_render_str_7x5("DEADBEEF", 1, 5, 1, 1, 1, 0, 0, 0);

	render_score();

	// TIM1 for other updates

	RCC->APB2ENR |= RCC_APB2ENR_TIM1EN;
	TIM1->DIER  = TIM_DIER_UIE;
	TIM1->PSC   = 48000 - 1;
	TIM1->ARR   = 200 - 1;
	TIM1->CR1 |= TIM_CR1_CEN;
	NVIC->ISER[0] |= (1 << TIM1_BRK_UP_TRG_COM_IRQn);

	NVIC_SetPriority(TIM1_BRK_UP_TRG_COM_IRQn, 3);

	for(;;);
}

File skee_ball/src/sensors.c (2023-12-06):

/**
  ******************************************************************************
  * @file    sensor.c
  * @author  Ac6
  * @version V1.0
  * @date    01-December-2013
  * @brief   .
  ******************************************************************************
*/


#include "stm32f0xx.h"
#include "sensors.h"

void sensors_enable() {
	NVIC_EnableIRQ(EXTI4_15_IRQn);
}

void sensors_disable() {
	NVIC_DisableIRQ(EXTI4_15_IRQn);
}

void sensors_init() {
    // init GPIOB
    RCC -> AHBENR |= RCC_AHBENR_GPIOBEN;
    GPIOB->MODER &= ~(GPIO_MODER_MODER8  | GPIO_MODER_MODER9  |
                      GPIO_MODER_MODER10 | GPIO_MODER_MODER11 |
                      GPIO_MODER_MODER12 | GPIO_MODER_MODER13 |
                      GPIO_MODER_MODER14);
    GPIOB->PUPDR |= GPIO_PUPDR_PUPDR8_1  | GPIO_PUPDR_PUPDR9_1  |
                    GPIO_PUPDR_PUPDR10_1 | GPIO_PUPDR_PUPDR11_1 |
                    GPIO_PUPDR_PUPDR12_1 | GPIO_PUPDR_PUPDR13_1 |
                    GPIO_PUPDR_PUPDR14_1;

    // init exti
    RCC -> APB2ENR |= RCC_APB2ENR_SYSCFGCOMPEN;
    //change to number or port to
    SYSCFG -> EXTICR[2] |= (SYSCFG_EXTICR3_EXTI8_PB  | SYSCFG_EXTICR3_EXTI9_PB |
                            SYSCFG_EXTICR3_EXTI10_PB | SYSCFG_EXTICR3_EXTI11_PB);
    SYSCFG -> EXTICR[3] |= (SYSCFG_EXTICR4_EXTI12_PB | SYSCFG_EXTICR4_EXTI13_PB |
                            SYSCFG_EXTICR4_EXTI14_PB);
    EXTI->RTSR &= ~(EXTI_RTSR_TR8  | EXTI_RTSR_TR9  | EXTI_RTSR_TR10 |
                    EXTI_RTSR_TR11 | EXTI_RTSR_TR12 | EXTI_RTSR_TR13);
    EXTI->FTSR |= (EXTI_FTSR_TR8  | EXTI_FTSR_TR9  | EXTI_FTSR_TR10 |
                   EXTI_FTSR_TR11 | EXTI_FTSR_TR12 | EXTI_FTSR_TR13);
    EXTI -> RTSR |= EXTI_RTSR_TR14;

    EXTI -> IMR |= (EXTI_IMR_MR8  | EXTI_IMR_MR9  | EXTI_IMR_MR10 | EXTI_IMR_MR11 |
                    EXTI_IMR_MR12 | EXTI_IMR_MR13 | EXTI_IMR_MR14);
    NVIC_SetPriority(EXTI4_15_IRQn, 3);
    sensors_enable();
}

void EXTI4_15_IRQHandler() {
    uint32_t PR = EXTI->PR; // slight optimization for volatile

    if (PR & EXTI_PR_PR8) {
        sensors_scored(Score_10);
        EXTI -> PR = EXTI_PR_PR8;

    } else if (PR & EXTI_PR_PR9) {
        sensors_scored(Score_10);
        EXTI -> PR = EXTI_PR_PR9;

    } else if (PR & EXTI_PR_PR10) {
        sensors_scored(Score_20);
        EXTI -> PR = EXTI_PR_PR10;

    } else if (PR & EXTI_PR_PR11) {
        sensors_scored(Score_30);
        EXTI -> PR = EXTI_PR_PR11;

    } else if (PR & EXTI_PR_PR12) {
        sensors_scored(Score_50);
        EXTI -> PR = EXTI_PR_PR12;

    } else if (PR & EXTI_PR_PR13) {
        sensors_scored(Score_50);
        EXTI -> PR = EXTI_PR_PR13;

    } else if (PR & EXTI_PR_PR14) {
        sensors_scored(Score_Gutter);
        EXTI -> PR = EXTI_PR_PR14;

    }
}

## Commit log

2023-09-06 Inital HUB75 Code
    [HUB75Lib.cfg]
2023-09-14 changed font size to 7x5, implemented fix for direction of font rendering, implemented fix for suboptimal brigtness.
    [HUB75.c, main.c]
2023-09-25 Added schematic and imported microcontroller symble and footprint
    [Schematic.kicad_pcb, Schematic.kicad_sch]
2023-09-26 Added Schematic Backups to gitignore
2023-09-26 Added paritial schematic including microprocessor, hub75 and keypad
    [Schematic.kicad_pcb, Schematic.kicad_sch, hub75.kicad_sch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]
2023-09-26 updated schematic overall view
2023-09-26 Added power supply.
    [EDI2CAP.CFG, INDPM120120X1020N.PcbLib, LM2678 - 5.0V.kicad_pcb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]
2023-09-27 Added audio circuitry
    [Audio AMP.kicad_pcb, Audio AMP.kicad_sch, Schematic.kicad_sch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]
2023-09-29 fixed power circuit
    [LM2678 - 5.0V.kicad_sch]
2023-10-03 modified power control to remove old regulator
    [LM2678 - 5.0V.kicad_pcb]
2023-10-03 initial CB design
    [EDI2CAP.CFG, INDPM120120X1020N.PcbLib, MSS1210-103MEB.SchLib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]
2023-10-03 Most of the schematic and PCB layout.
    [Schematic.kicad_pcb, Schematic.kicad_sch, hub75.kicad_sch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]
2023-10-04 Added stuff from today
    [Schematic.kicad_pcb, Schematic.kicad_sch, audio.kicad_sch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]
2023-10-05 Added sensors. Fixed other stuff.
    [Schematic.kicad_pcb, Schematic.kicad_sch, audio.kicad_sch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]
2023-10-07 initially added sensors.
    [sensor.kicad_pcb, sensor.kicad_sch]
2023-10-07 Mostly finallized PCB
    [Schematic.kicad_pcb, audio.kicad_sch, hub75.kicad_sch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]
2023-10-10 Added images
    [Schematic.kicad_pcb, audio.kicad_sch, hub75.kicad_sch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]
2023-10-12 Added Cap to osilator, and fixed posible issues with signals near it.
    [Schematic.kicad_pcb, audio.kicad_sch, hub75.kicad_sch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]
2023-10-12 fixed exporting script
    [Schematic.kicad_pcb]
2023-10-12 Updated svg's
    [Schematic.kicad_pcb]
2023-10-13 Implemented some suggestions from presentation. Power trace size, reset button position, mounting holes, copper fill near edge, WS Data moved, removed debuge LED and analog vias.
    [Schematic.kicad_pcb]
2023-10-13 Forgot to save the schematic from the last commit.
    [hub75.kicad_sch, mcroprocessor.kicad_sch]
2023-10-18 Lab fixes
    [Schematic.kicad_pcb, keypad.kicad_sch, sensors.kicad_sch]
2023-10-19 Added level shifter (may or may not use) other minor fixes
    [Schematic.kicad_pcb, Schematic.kicad_sch, hub75.kicad_sch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]
2023-10-19 relabeld all of the components so they have more resonable numbers
    [Schematic.kicad_pcb, audio.kicad_sch, hub75.kicad_sch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]
2023-10-20 fixed LM385 not having voltage div, and ploted plots.
    [Schematic-B_Cu.gbl, Schematic-B_Mask.gbs, Schematic-B_Paste.gbp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]
2023-10-22 Added WS2812BLib and fixed some issues with Used Resources.txt
    [New_configuration (3).cfg, WS2812BLib.cfg]
2023-11-02 Added SoundLib
    [SoundLib.cfg]
2023-11-02 began interation. Both HUB75 and Sound working
    [integration.cfg]
2023-11-08 Update keypad.c
    need to swap pb0-3 and pb4-7
    [keypad.c]
2023-11-10 added sensor code, started on some game logic
2023-11-10 finished integrating sensors
2023-11-10 Working Normal and Time Attack modes with display and sensors.
    [skee_ball.cfg]
2023-11-30 Fixed font, fixed some issues with ws2812b, finished implementation
    [HUB75.c, main.c, ws2812b.c]
2023-12-06 few minor additions such as mute, soft power off, and replay. Fixed interupt priority.
    [SoundLib.c, main.c, sensors.c]
